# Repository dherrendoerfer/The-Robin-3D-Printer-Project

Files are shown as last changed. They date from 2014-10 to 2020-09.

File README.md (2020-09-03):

Copyright (C) 2014,2015,2016,2017 D.Herrendoerfer



# The-Robin-3D-Printer-Project

The Robin 3D printers share the goal to be simple to build, based on a simple and
repeatable principle, and consist of parts that can be produced with smaller 3D printers.

### Robin
A simple to build 3D printer with a combined X/Y stage.
This printer can be used with very high accuracy as well as with very heavy print head assemblies,
because the print head does not move except in the Z-direction.

( Robin is licensed under Creative Commons CC0 )

### Robin Plus
The Rob Plus 3D printer is build with an inverted-H-assembly, not unlike a coreXY setup, but
all steppers are connected along a single line, giving the printer a sleek but sturdy frame.
Hence the name Robin Plus - the timing belt forms the plus shape.
The Z-Axis can be built with either a single or a double-sided crane. The double-sided setup
is much less prone to vibrations, while the single-sided setup is very simple and good to
use as an educational example.

( Robin Plus is licensed under Creative Commons CC0 )

### Bad Robin
Bad Robin is the smaller brother of the Big Bad Robin 3D printer. Both printers share the same
parts, only the aluminium profiles and the linear rails change in size - all other parts stay the same.
Bad Robin has a very low parts count, a high resolution and can go very fast. It is also very affordable
with the 250mm rails version costing around 250 Euros in non-printed parts.

( Bad Robin is licensed under GPLv2 )  
The Bad Robin project got its own repo and now lives here:  
https://github.com/dherrendoerfer/The-Bad-Robin-3D-Printer

## Images

### Robin:





### Robin Plus:









Donations:  
If you would like to make a donation to keep this project and others going you can do so at:  
https://www.paypal.me/dherrendoerfer  
This helps a lot !

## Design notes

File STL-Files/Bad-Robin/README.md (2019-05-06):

# The Bad Robin project files have moved to a new home:

https://github.com/dherrendoerfer/The-Bad-Robin-3D-Printer

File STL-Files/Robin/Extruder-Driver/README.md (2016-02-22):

The-Robin-3D-Printer-Bowden-Driver
==================================

This extruder driver is for use with the E3D MK8 drive gear
and an NEMA 17 stepper motor. The bearing is a standart type 608
8x22x7 Skateboard bearing. Furthermore a M3 Screw and a 5x3 rubber
gasket (or a small spring) are needed.

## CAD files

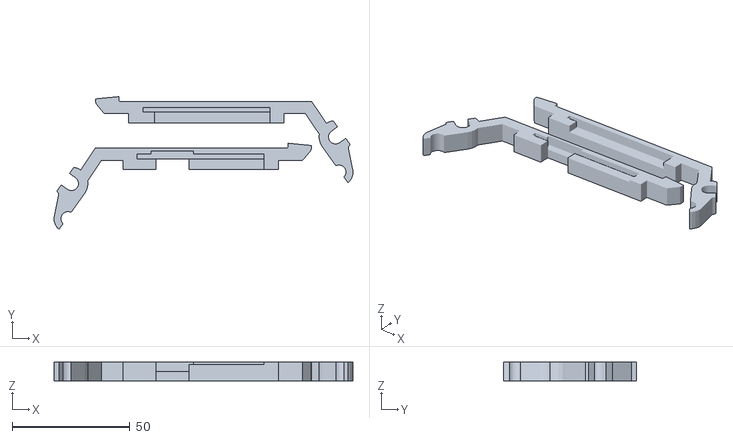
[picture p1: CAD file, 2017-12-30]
STL-Files/Robin-Plus/Rob-3D-RampsMount.stl
127.1 x 56.4 x 8.00

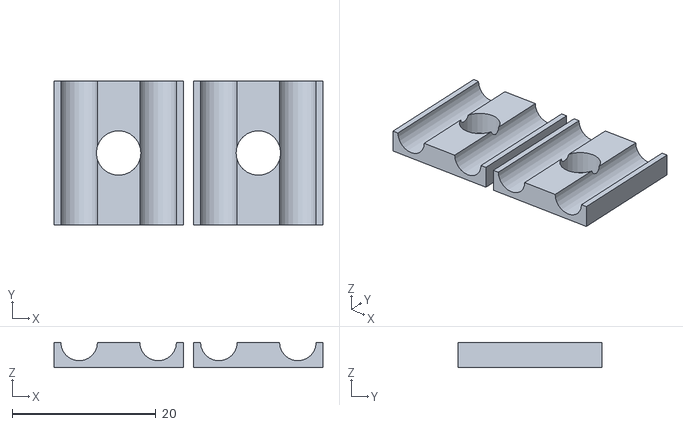
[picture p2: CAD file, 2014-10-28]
STL-Files/Robin/5mm/Extruder-Mount/Robin-Extruder-Mount-4.stl
37.5 x 20.0 x 3.50

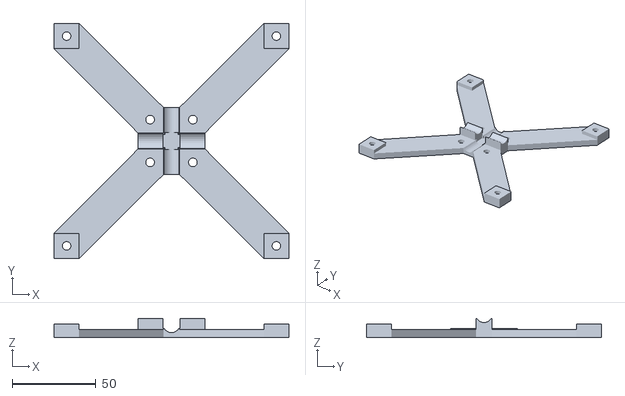
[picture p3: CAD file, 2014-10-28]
STL-Files/Robin/5mm/Table/Robin-Table-2.stl
140.0 x 140.0 x 11.5

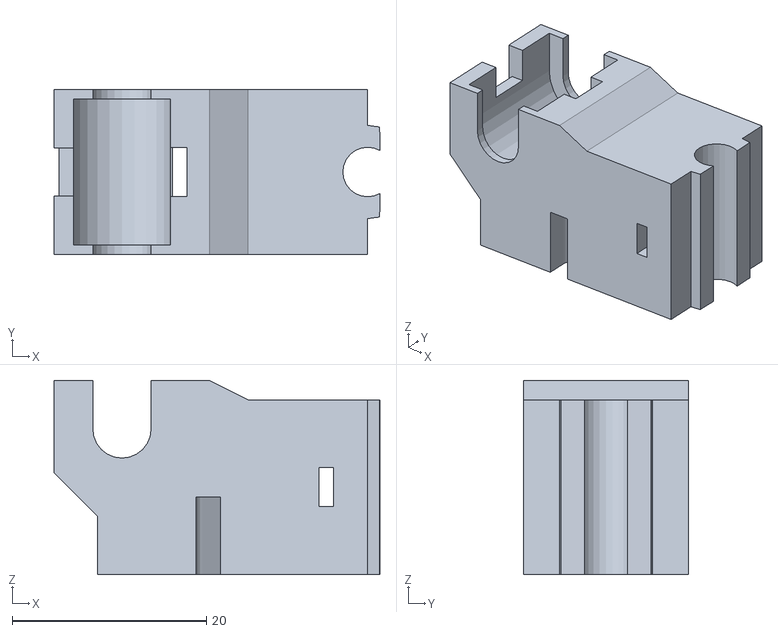
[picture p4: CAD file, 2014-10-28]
STL-Files/Robin/5mm/XY-Axis/Robin-Y-Arm-1.stl
33.6 x 17.0 x 20.0

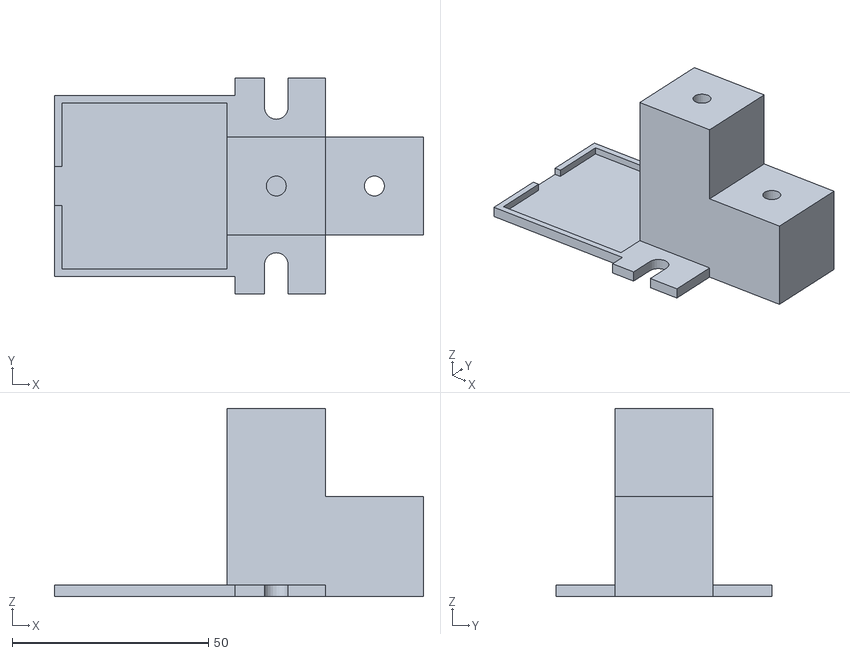
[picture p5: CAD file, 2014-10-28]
STL-Files/Robin/5mm/Z-Axis/Robin-Z-Axis-1.stl
94.0 x 55.0 x 48.0

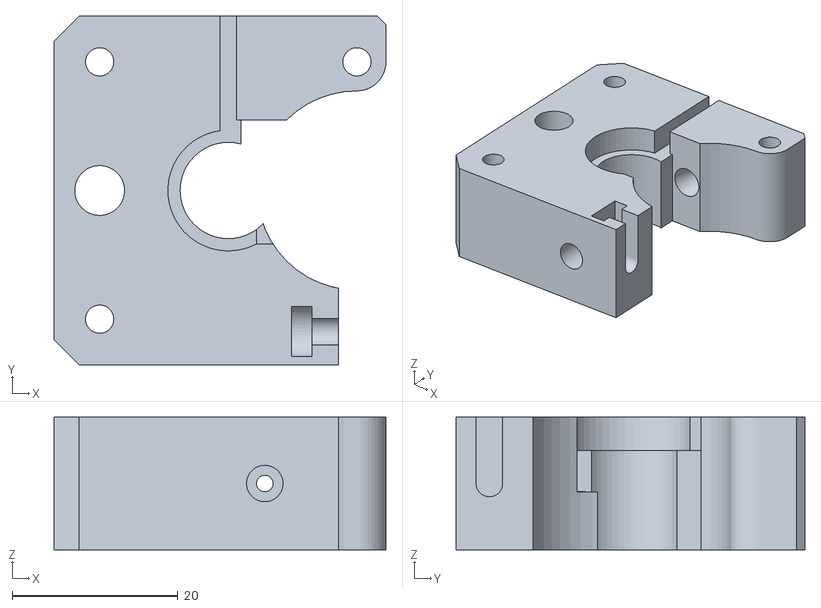
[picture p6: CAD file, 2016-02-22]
STL-Files/Robin/Extruder-Driver/Robin-Bowden-Driver-Mid.stl
40.0 x 42.0 x 16.0

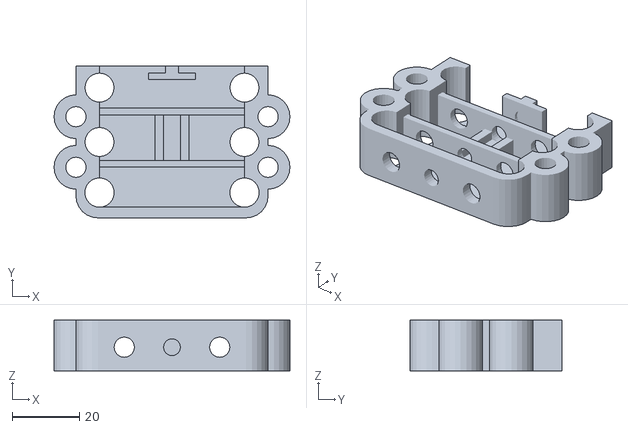
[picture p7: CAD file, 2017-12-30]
STL-Files/Robin-Plus/Rob-3D-Table-Z-Rod.stl
70.0 x 45.0 x 15.0

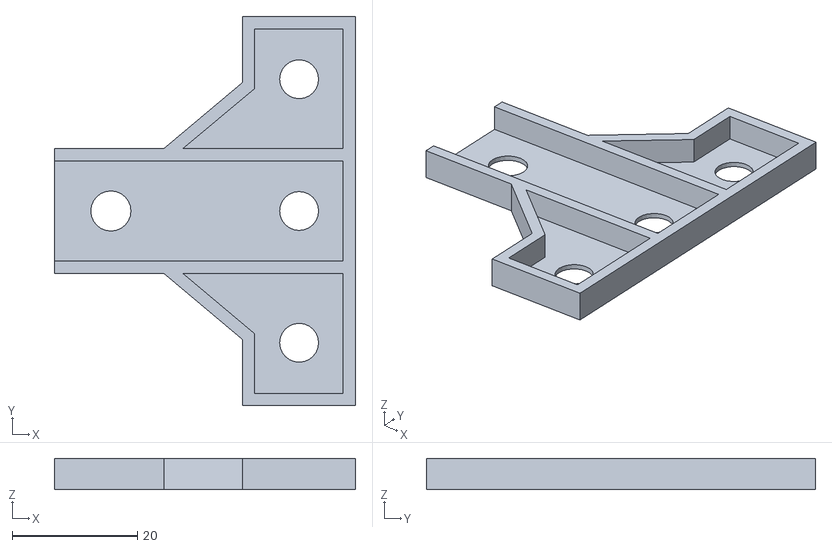
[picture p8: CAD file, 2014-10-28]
STL-Files/Robin/5mm/Extruder-Mount/Robin-Extruder-Mount-2.stl
48.0 x 62.0 x 5.00

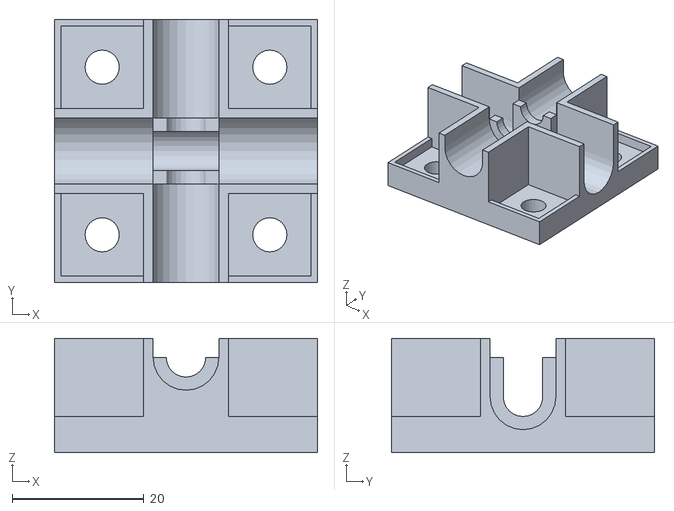
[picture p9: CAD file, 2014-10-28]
STL-Files/Robin/5mm/Table/Robin-Table-1.stl
40.0 x 40.0 x 17.4

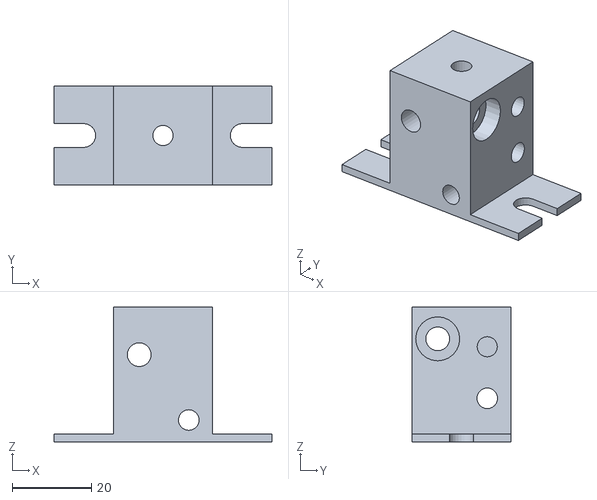
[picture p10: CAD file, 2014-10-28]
STL-Files/Robin/5mm/XY-Axis/Robin-Blocks-3.stl
55.0 x 25.0 x 34.0

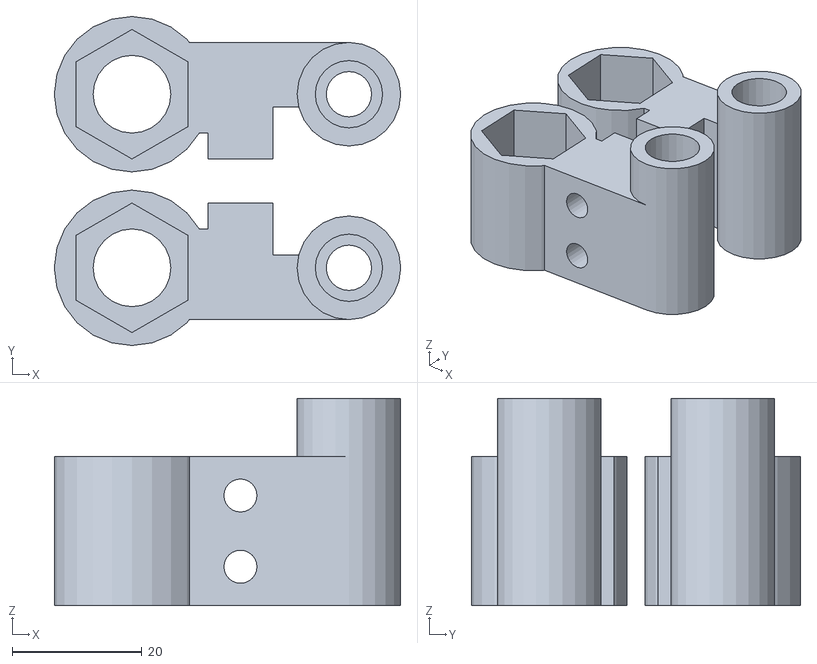
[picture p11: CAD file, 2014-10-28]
STL-Files/Robin/5mm/Z-Axis/Robin-Z-Axis-3a.stl
53.5 x 50.8 x 32.0

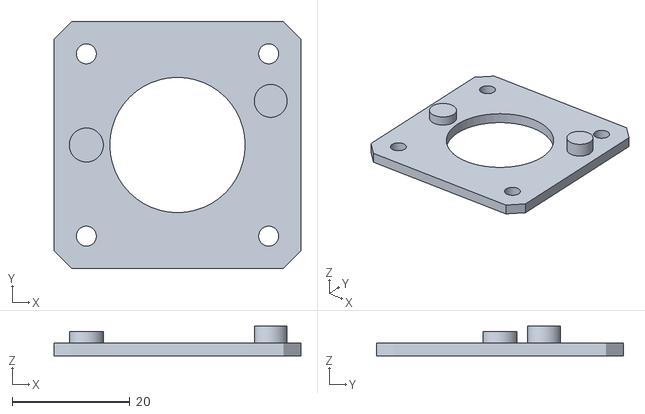
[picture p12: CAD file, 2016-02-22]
STL-Files/Robin/Extruder-Driver/Robin-Bowden-Driver-Bottom.stl
42.0 x 42.0 x 5.10

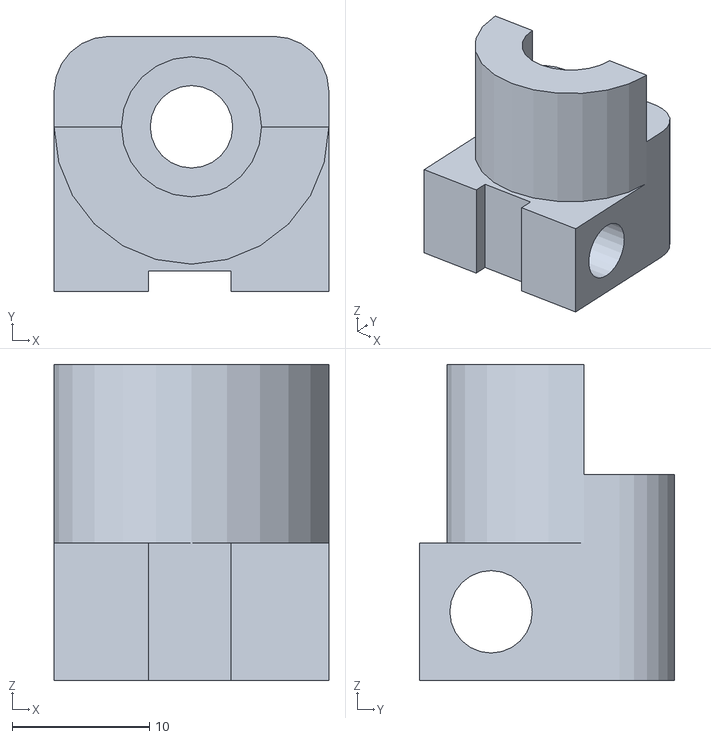
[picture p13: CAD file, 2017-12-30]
STL-Files/Robin-Plus/Rob-3D-Krane1.stl
20.0 x 18.6 x 23.0

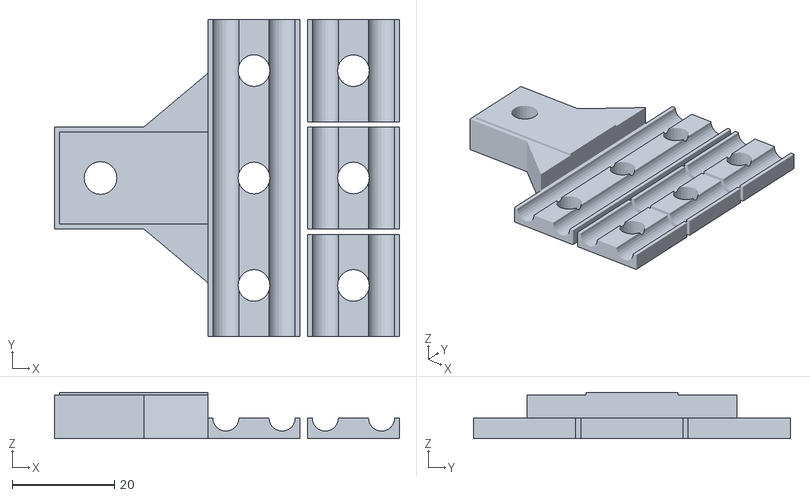
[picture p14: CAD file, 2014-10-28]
STL-Files/Robin/5mm/Extruder-Mount/Robin-Extruder-Mount-1.stl
67.4 x 62.0 x 9.00

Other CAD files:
STL-Files/Robin/5mm/XY-Axis/Robin-Blocks-2.stl
STL-Files/Robin/5mm/Z-Axis/Robin-Z-Axis-3b.stl
STL-Files/Robin/Extruder-Driver/Robin-Bowden-Driver-Idler-1.stl
STL-Files/Robin-Plus/Rob-3D-Stand1.stl
STL-Files/Robin-Plus/Rob-3D-Extruder.stl
STL-Files/Robin-Plus/Rob-3D-Extruder1.stl
STL-Files/Robin-Plus/Rob-3D-Krane2.stl
STL-Files/Robin-Plus/Rob-3D-Krane3.stl
STL-Files/Robin-Plus/Rob-3D-Post-w-Power.stl
STL-Files/Robin-Plus/Rob-3D-Stand2.stl
STL-Files/Robin-Plus/Rob-3D-Switches1.stl
STL-Files/Robin-Plus/Rob-3D-Table-H-MotCase.stl
STL-Files/Robin-Plus/Rob-3D-Table-H-Parts.stl
STL-Files/Robin-Plus/Rob-3D-Table-Z-Mot.stl
STL-Files/Robin-Plus/Rob-3D-Table-Z-Top.stl
STL-Files/Robin/5mm/Extruder-Mount/Robin-Extruder-Mount-3.stl
STL-Files/Robin/5mm/XY-Axis/Robin-Blocks-1.stl
STL-Files/Robin/5mm/XY-Axis/Robin-Blocks-4.stl
STL-Files/Robin/5mm/XY-Axis/Robin-Stepper-Mount-1.stl
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

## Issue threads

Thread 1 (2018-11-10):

Software Download?

olikraus, 2018-11-10:
Hi

Danke für das nette Gespräch von vorhin auf der Mini Make.
Aber: Wo gibt es denn die von Dir angesprochene modifizierte Software für den Bad Robin?
Ich hab hier leider keinen Link gefunden.

Danke, Oliver

dherrendoerfer, 2018-11-11:
Die Firmware ist hier zu finden:
https://github.com/dherrendoerfer/The-Robin-3D-Printer-Project/tree/master/STL-Files/Bad-Robin/Firmware

olikraus, 2018-11-11:
:+1: Danke

Closed 2018-11-11.

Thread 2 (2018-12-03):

"ITEM 40mm aluminium profile"?

olikraus, 2018-12-03:
Hallo (ich schon wieder)

Was ist denn das "ITEM 40mm aluminium profile"?

Ist damit das Profile 8 gemeint?
https://product.item24.de/produkte/produktkatalog/products/konstruktionsprofile-8-1001042794/

Genauer: Das Profile 8 40x40 leicht, natur?

Danke & Grüße
Oliver

dherrendoerfer, 2018-12-04:
Ja, ich kaufe immer das hier:
https://www.ebay.de/itm/ALU-Profil-Aluprofil-40x40-Nut-8-Aluminium-Profil-AlClipTec-item-kompatibel/261818937804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

Ich habe uebrigens z.Zt. seed-Kits (gruen), und es wird am JFZ eine Sammelbestellung Anfang 2019 geben.

olikraus, 2018-12-04:
Ah guter link.

Was ist denn ein seed-Kit?

Mein größtes Problem sind eigentlich noch die auszudruckenden Teile vom Bad-Robin.

naja, auch für den "Timing belts with 2xdriver (T2)" hab ich noch keine bezugsquelle gefunden.

Wie kommt denn das JFZ an die geprintenten Teile?

dherrendoerfer, 2018-12-04:
Ein seed-kit ist ein Komplett-Set der gedruckten Teile. Diese sind leicht zu erkennen, weil sie grell grün sind. Wer ein seed-kit  bekommt verspricht mir im Gegenzug mindestens zwei Kits zurückzugeben, damit ich sie weitergeben kann.
Das JFZ bekommt Teile z. Zt. auch von mir.

olikraus, 2018-12-04:
ahhh... das wäre also genau das was ich bräuchte :-)

Das hört sich nach einem guten Deal an. Also, ich wäre dabei. Dann würde ich mal in den nächsten Tagen das BOM zusammenstellen (inkl. Bezugsquellen) und mich dann nochmal melden?

mein e-mail ist übrigens: olikraus_@_gmail_._com (ohne _)

olikraus, 2018-12-05:
Ich habe jetzt gestern das zugehörige Video angeschaut. Soweit ist (fast) alles klar. Drei Fragen habe ich noch:
1. Der verwendete PTFE Tube: Innendurchmesser müsste 2mm sein, aber welchen aussendurchmesser hat denn der denn? 4mm?
2. Die NEMA17 motoren: Die gibt es in verschiedenen Stärken und Tiefen. Ich habe mal diesen hier ausgesucht:https://www.ebay.com/itm/Nema-17-Stepper-Motor-Bipolar-42mm-Hybrid-Two-Phase-42SHD0001-24-For-3D-Printer/332871755225
Wäre der ok?

Nun ja, wenn ich das Seed-Kit von Dir bekomme, würde ich mal loslegen mit der Bestellung.

dherrendoerfer, 2019-01-02:
Solved.

Closed 2019-01-02.

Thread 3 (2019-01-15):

z-axis m8 rod: BOM updates

olikraus, 2019-01-15:
Please excause another update request.

"1x Threaded rod TR8 350mm long"

The actual length depends on the shaft length of the stepper motor. Maybe I have a stepper motor with long shaft, but for my setup, the rod must be only 340mm. I think it would be ok for any shaft length if the rod has only 340mm, so the update is to change the BOM entry to: "1x Threaded rod TR8 **340mm** long"

"1x Threaded rod nut TR8"

Actually this is a "long nut" with at least 12mm length. It would be cool if this is also mentioned: "1x Threaded rod **long** nut TR8 **with a minimal length of 12mm**"

Metal ball is not mentioned.

The metal ball (steel ball) which is placed below the M8 rod is not mentioned. At least it should be mentioned that either a bearing or the metal ball (3..5mm) has to be sourced:
"Z-axis bearing ball solution: 1x Bike stainless steel ball 3.5 to 4.5mm diameter"

dherrendoerfer, 2019-01-15:
Thanks @olikraus
I'll update this:

the correct length of the rod is 315mm when using the steel ball, and 320mm when using the bearing.
The TR8 Nut should be 17mm, or at least 12mm high
One steel ball bearing ball with 3.5 to 4.5mm diameter.

dherrendoerfer, 2019-01-16:
I updated the BOM document, closing.

Closed 2019-01-16.

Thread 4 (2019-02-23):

extruder heater and fan connection

olikraus, 2019-02-23:
I am a little bit confused.
As per the video, the extruder heater is connected to D10 and the fan to D9.

In the md file https://github.com/dherrendoerfer/The-Robin-3D-Printer-Project/blob/master/STL-Files/Bad-Robin/Build-Instructions.md the following is mentioned:

> Connect the extruder heater to E0
> Connect the extruder fan to E1, watch the polarity !

Probably it means the same because the heater of the first extruder is connected to D10. However, calling the first extrude E0 is also a little bit misleading, because the picture here https://reprap.org/wiki/File:Rampswire14.svg calls it extruder 1.

Suggestion is to change the description in the build instructions:

> Connect the extruder heater to D10
> Connect the extruder fan to D9, watch the polarity !

dherrendoerfer, 2019-02-25:
Fixed with commit: https://github.com/dherrendoerfer/The-Robin-3D-Printer-Project/commit/65b15908f6b379d16c3a0390eba980823d689b62

Closed 2019-02-25.

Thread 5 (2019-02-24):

Inductive proximity sensor output to Zmax should go through a 10K to 15K resistor

olikraus, 2019-02-24:
As stated in part 22 of the instructions (https://github.com/dherrendoerfer/The-Robin-3D-Printer-Project/blob/master/STL-Files/Bad-Robin/Build-Instructions.md) the level probe (Inductive proximity sensor) signal output should be connected to the z-max pin directly.

However, this is dangerous:
1) The RAMPS board directly connects the z-max input pin with the uC without further protection.
2) The level probe sensor will deliver 12v as a active high signal, which will destroy the internal protection diode.

See also: https://www.avrfreaks.net/forum/12-volt-input-sigal-atmel-pin-make-logic-high

The signal output of the level probe sensor (usually the black line) should go to a 10K resistor, the other end of the 10K resistor is then connected to the z-max input of the RAMPS board.

This means, instead of
```
Connect the home switches

    X home switch to Xmin pin.
    Y home switch to Ymin pin.
    Z level probe (output) to Zmax
```

the description should be this:

```
Connect the home switches.

    X home switch to Xmin pin.
    Y home switch to Ymin pin.
    Z level probe (output, black line) to Zmax via 10K resistor
```

Additionally, the BOM should mention the 10K resistor. BTW: The home switches are also not mentioned in the BOM.

olikraus, 2019-02-24:
I have ordered exactly an "Inductive proximity switch PNP, NO(normally open)". The sensor, which I have received behaves exactly like a PNP senser. However:
 * I have to add an extra 10K resistor to protect the ATMega
 * I have to reconfigure the firmware
 * I have to add an external pull-down resistor

In other words, the BOM is wrong: Your 3D printer requires a NPN version of this senser. If it is a NPN version, then indeed no further resistor is required. However, the PNP senser, connected in the way as described in your video, will destroy the ATMega board (unless the 10K resistor is used).

dherrendoerfer, 2019-02-25:
I fixed the BOM, I (in fact) did use a NPN, just copied it wrong.

So: If you have a PNP -> The above is the correct way to make it work .
Thanks!

olikraus, 2019-02-25:
:+1:

olikraus, 2019-03-03:
Just a small note:
for my PNP NO senser, i have a 100K pull-down and a 10K resistor in the dataline itself.

For this, I had to change the configuration (Configuration.h) like this:
```
#define ENDSTOP_PULLUP_Z_MIN false
#define ENDSTOP_Z_MIN_INVERTING false
...
#define ENDSTOP_Z_BACK_ON_HOME 1
```

Closed 2019-02-25.

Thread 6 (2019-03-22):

BOM List and RAMPs question

mmonti, 2019-03-22:
Hi Dirk,

Thanks so much for sharing your work. I am totally doing this printer. I put together an excel sheet with some links based on the materials you provided in the docs:
* https://docs.google.com/spreadsheets/d/1-j1_p4K47khKqKf07HFRd5YxoagGtwe-34txlghNuE4/edit?usp=sharing

I have a couple questions for you:
- What RAMPs kit do you use?
I am newbie on this and looking for RAMPs kits is overwhelming the amount of versions I found. I am not really sure which one to buy.
- How do you power the printer?

Thanks!,
Mauro.-

Closed 2019-04-02.

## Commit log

2014-10-28 Added initial stl files for the X and Y axis
    [Robin-Blocks-1.stl, Robin-Blocks-2.stl, Robin-Blocks-3.stl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]
2014-10-28 Also add Z-Axis stl files
    [Robin-Z-Axis-1.stl, Robin-Z-Axis-2.stl, Robin-Z-Axis-3a.stl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]
2014-10-28 Add the extruder mount files
    [Robin-Extruder-Mount-1.stl, Robin-Extruder-Mount-2.stl, Robin-Extruder-Mount-3.stl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]
2016-02-22 Add extruder driver again.
    [Robin-Bowden-Driver-Bottom.stl, Robin-Bowden-Driver-Idler-1.stl, Robin-Bowden-Driver-Idler-2.stl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]
2017-12-30 Update project stl files, and add Robin Plus files.
    [Rob-3D-Extruder.stl, Rob-3D-Extruder1.stl, Rob-3D-Krane1.stl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]
2018-05-06 Add files for Bad Robin update documentation
    [BR-v1-Display_Holder.stl, BR-v1-Fan_Shroud.stl, BR-v1-Foot.stl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]
2018-05-06 Push missing files, add to BOM
2018-06-09 Add Z Idler without bearing and lathe work requirement
    [BR-v1-Z_Idler_nobearing.stl]
2018-07-22 Update Instructions and add Mount w. switch block
    [BR-v1-Hotend_Mount-A.stl]
2018-12-06 Update Bill-of-materials.md
    Add coupler to bom
2019-02-24 Fix error in BOM
2019-05-06 Move the Bad Robin repo
    [BR-v1-Display_Holder.stl, BR-v1-Fan_Shroud.stl, BR-v1-Foot.stl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]
